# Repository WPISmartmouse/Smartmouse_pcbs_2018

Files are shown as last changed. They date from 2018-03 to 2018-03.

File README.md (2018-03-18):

# BRO Submission README

 - Schematics are included as pdfs
 - BOM is inclded as an excel spreadsheet (some items are approximate)
 - General maze solving methodology is described below

We use a flood-fill algorithm to solve the maze. We explore by taking the optimistic assuming there are no walls other than the ones we have observed up until that point, and replan our next step at each cell. We can return once the center is reached and continue to explore for faster routes as we traverse more of the maze until time runs out or the shortest path is found.

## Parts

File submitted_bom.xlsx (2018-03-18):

Manufctr Part # | Description | Source | Quantity | Cost Per Item | Extended Cost | Purchased | Link for Purchasing | Datasheet | Shipping Included? | Notes
 | 2c Lipo battery | Hobby King | 2 | $7.660 | $15.32 | Y | https://hobbyking.com/en_us/turnigy-nano-tech-1500mah-2s-25-50c-lipo-pack.html |  | No
AS5048A | Magnet Sensor for Encoder | Mouser | 4 | $7.800 | $31.20 |  | https://www.mouser.com/ds/2/588/AS5048_DS000298_3-00-1100510.pdf |  | No | out of stock on Digikey
AS5000-MD6H-2 | Magnet for Encoder | AMS | 4 | $2.900 | $11.60 |  |  | http://ams.com/eng/content/download/14907/272250/12031 | No
 | capacitors | Digikey | 18 | $0.320 | $5.76 |  |  |  | No
 | resistors | Digikey | 22 | $0.050 | $1.10 |  |  |  | No
 | LEDs | Digikey | 16 | $0.400 | $6.40 |  |  |  | No
502443-0270 | CLIK-mate 2mm Pitch 1x2 pcb header | Mouser | 4 | $0.510 | $2.04 |  | https://www.mouser.com/ProductDetail/Molex/502443-0270 | https://www.mouser.com/ds/2/276/5024430270_sd-1074815.pdf | No
502439-0200 | CLIK-mate 2mm Pitch 1x2 crimp housing | Mouser | 4 | $0.150 | $0.60 |  | https://www.mouser.com/ProductDetail/Molex/502439-0200 | https://www.mouser.com/ds/2/276/5024390200_sd-1074810.pdf | No
502438-0100 | CLIK-mate 2mm Pitch terminals | Mouser | 12 | $0.110 | $1.32 |  | https://www.mouser.com/ProductDetail/Molex/502438-0100 | https://www.mouser.com/ds/2/276/5024380100_CRIMP_TERMINALS-179287.pdf | No
502382-0670 | CLIK-mate 1.25mm Pitch 1x6, small conn pcb header | Mouser | 4 | $0.680 | $2.72 |  | https://www.mouser.com/ProductDetail/Molex/502382-0670 | https://www.mouser.com/ds/2/276/5023820670_PCB_RECEPTACLES-179370.pdf | No
502380-0600 | CLIK-mate 1.25mm Pitch 1x6, small conn crimp housing | Mouser | 4 | $0.250 | $1.00 |  | https://www.mouser.com/ProductDetail/Molex/502380-0600?qs=sGAEpiMZZMvyL6eCuHiWiirOw4xo%2ffkY | https://www.mouser.com/ds/2/276/5023800600_CRIMP_HOUSINGS-179295.pdf | No
502382-0370 | CLIK-mate 1.25mm Pitch 1x3 small conn pcb header | Mouser | 14 | $0.540 | $7.56 |  | https://www.mouser.com/ProductDetail/Molex/502382-0370 | https://www.mouser.com/ds/2/276/5023820370_PCB_RECEPTACLES-179354.pdf | No
502380-0300 | CLIK-mate 1.25mm Pitch 1x3 small conn crimp housing | Mouser | 14 | $0.160 | $2.24 |  | https://www.mouser.com/ProductDetail/Molex/502380-0300 | https://www.mouser.com/ds/2/276/5023800300_CRIMP_HOUSINGS-179281.pdf | No
502381-0000 | CLIK-mate 1.25 mm Pitch crimp terminals | Mouser | 66 | $0.044 | $2.90 |  | https://www.mouser.com/ProductDetail/Molex/502381-0000-Loose-Piece | https://www.mouser.com/ds/2/276/5023810000_CRIMP_TERMINALS-179285.pdf | No | bulk discount woot woot
N/A | Teensy 3.6 | Digikey | 1 | $32.500 | $32.50 |  |  |  | No
drv8833 | dual H bridge motor driver | Digikey | 2 | $2.410 | $4.82 |  | https://www.digikey.com/product-detail/en/texas-instruments/DRV8833PWPR/296-29434-1-ND/2743171 | http://www.ti.com/lit/ds/symlink/drv8833.pdf | No
tps82130 | voltage regulator | Digikey | 2 | $5.030 | $10.06 |  | https://www.digikey.com/product-detail/en/texas-instruments/TPS82130SILR/296-47436-1-ND/7708896 | http://www.ti.com/lit/ds/symlink/tps82130.pdf | No
N/A | Mouser shipping | Mouser | 1 | $10.000 | $10.00
N/A | Hobby King shipping | Hobby King | 1 | $8.100 | $8.10
N/A | Digikey shipping | Digikey | 1 | $10.000 | $10.00 |  |  |  | Yes
N/A | Solarbotics RW2i Wheel |  | 2 | $3.950 | $7.90 |  | https://www.pololu.com/product/1127 |  |  | backordered on pololu, alternative is http://www.robotmarketplace.com/products/0-rw2i-3mm.html
VSLY5940 | IR Emitter | Digikey | 14 | $1.500 | $21.00 |  | https://www.digikey.com/products/en?keywords=VSLY5940 | https://www.vishay.com/docs/84240/vsly5940.pdf | No
BPV11F | IR Receiver | Digikey | 14 | $1.080 | $15.12 |  | https://www.digikey.com/products/en?x=0&y=0&lang=en&site=us&KeyWords=BPV11F | https://www.digikey.com/products/en?x=0&y=0&lang=en&site=us&KeyWords=BPV11F | No
 | Custom PCBs |  | 10 | $38.000 | $380.00
3073 | 50:1 Micro Metal Gearmotor HPCB 6V with Extended Motor Shaft | Pololu | 2 | $18.950 | $37.90 |  | https://www.pololu.com/product/3073
 |  |  |  |  | $0.00
 |  |  |  |  | $0.00
 |  |  |  |  | $0.00
 |  |  |  | TOTAL | $613.84

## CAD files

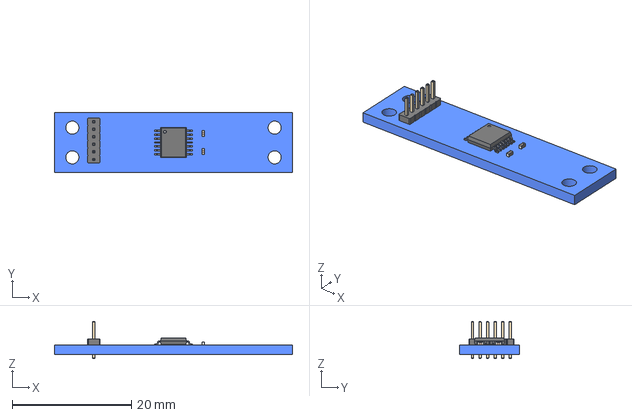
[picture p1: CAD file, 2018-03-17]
encoder_board/encoder_board.step
40.0 x 10.0 x 6.30 mm

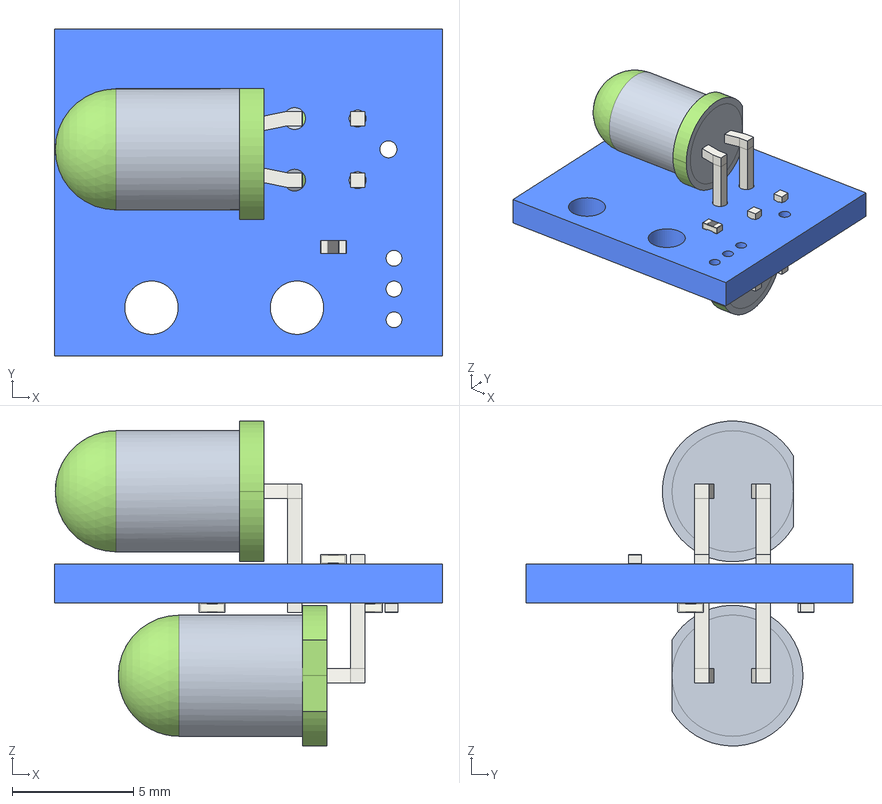
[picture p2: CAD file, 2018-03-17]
sensor_board/sensor_board.step
16.0 x 13.5 x 13.4 mm

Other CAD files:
encoder_board/encoder_board.FCStd
sensor_board/sensor_board.FCStd

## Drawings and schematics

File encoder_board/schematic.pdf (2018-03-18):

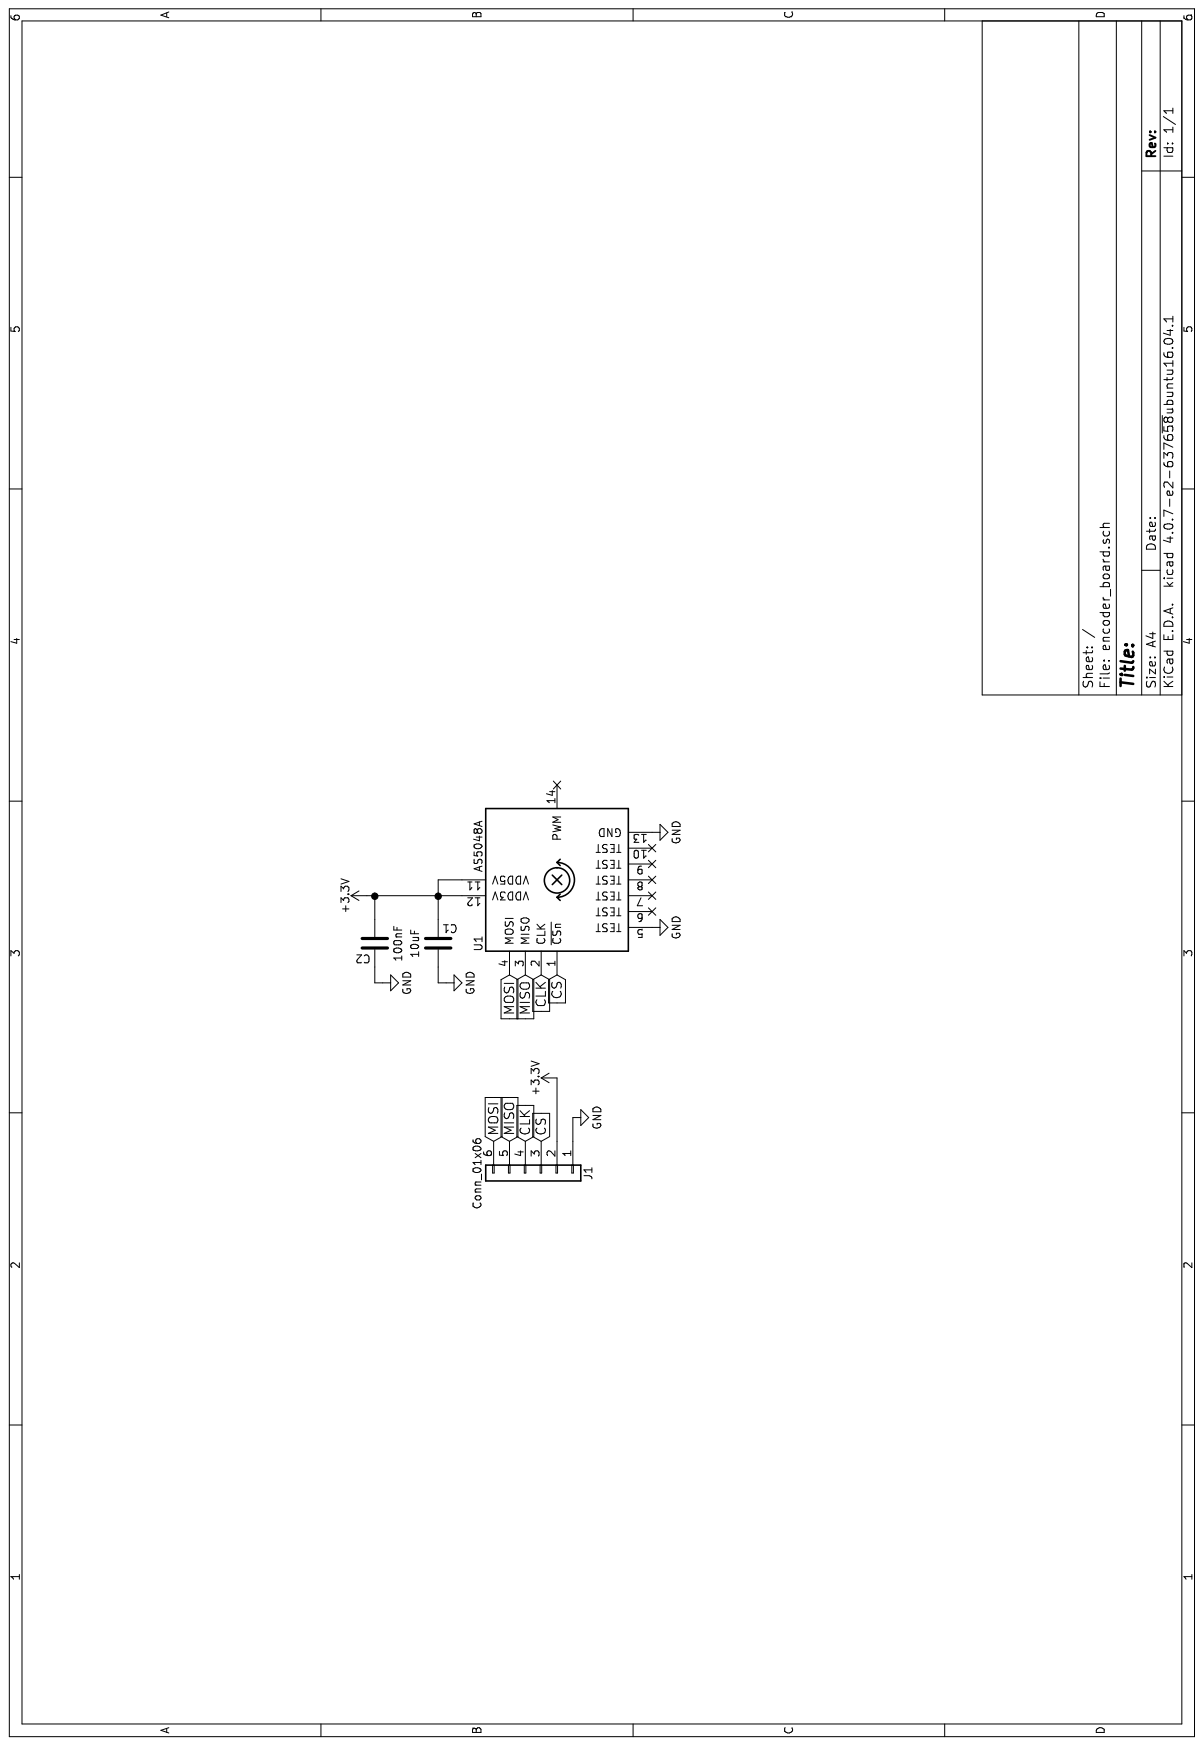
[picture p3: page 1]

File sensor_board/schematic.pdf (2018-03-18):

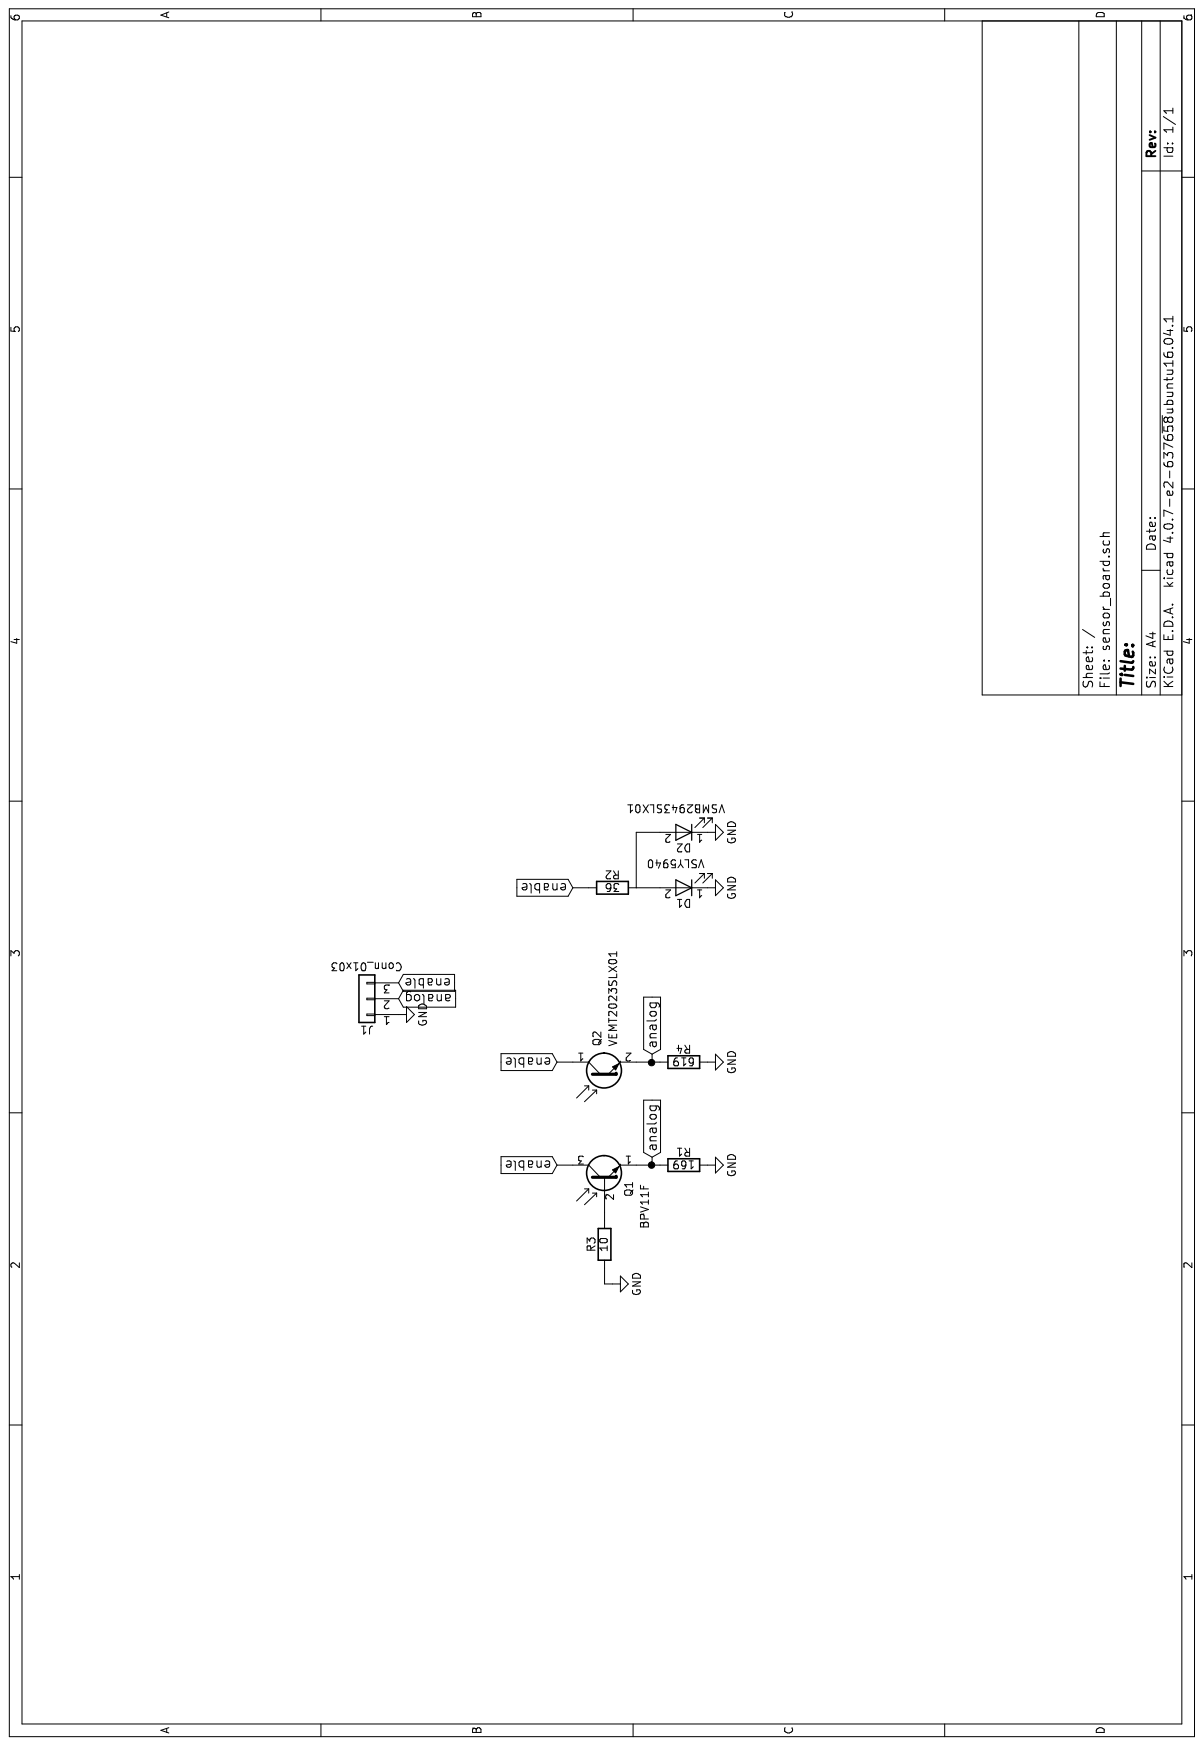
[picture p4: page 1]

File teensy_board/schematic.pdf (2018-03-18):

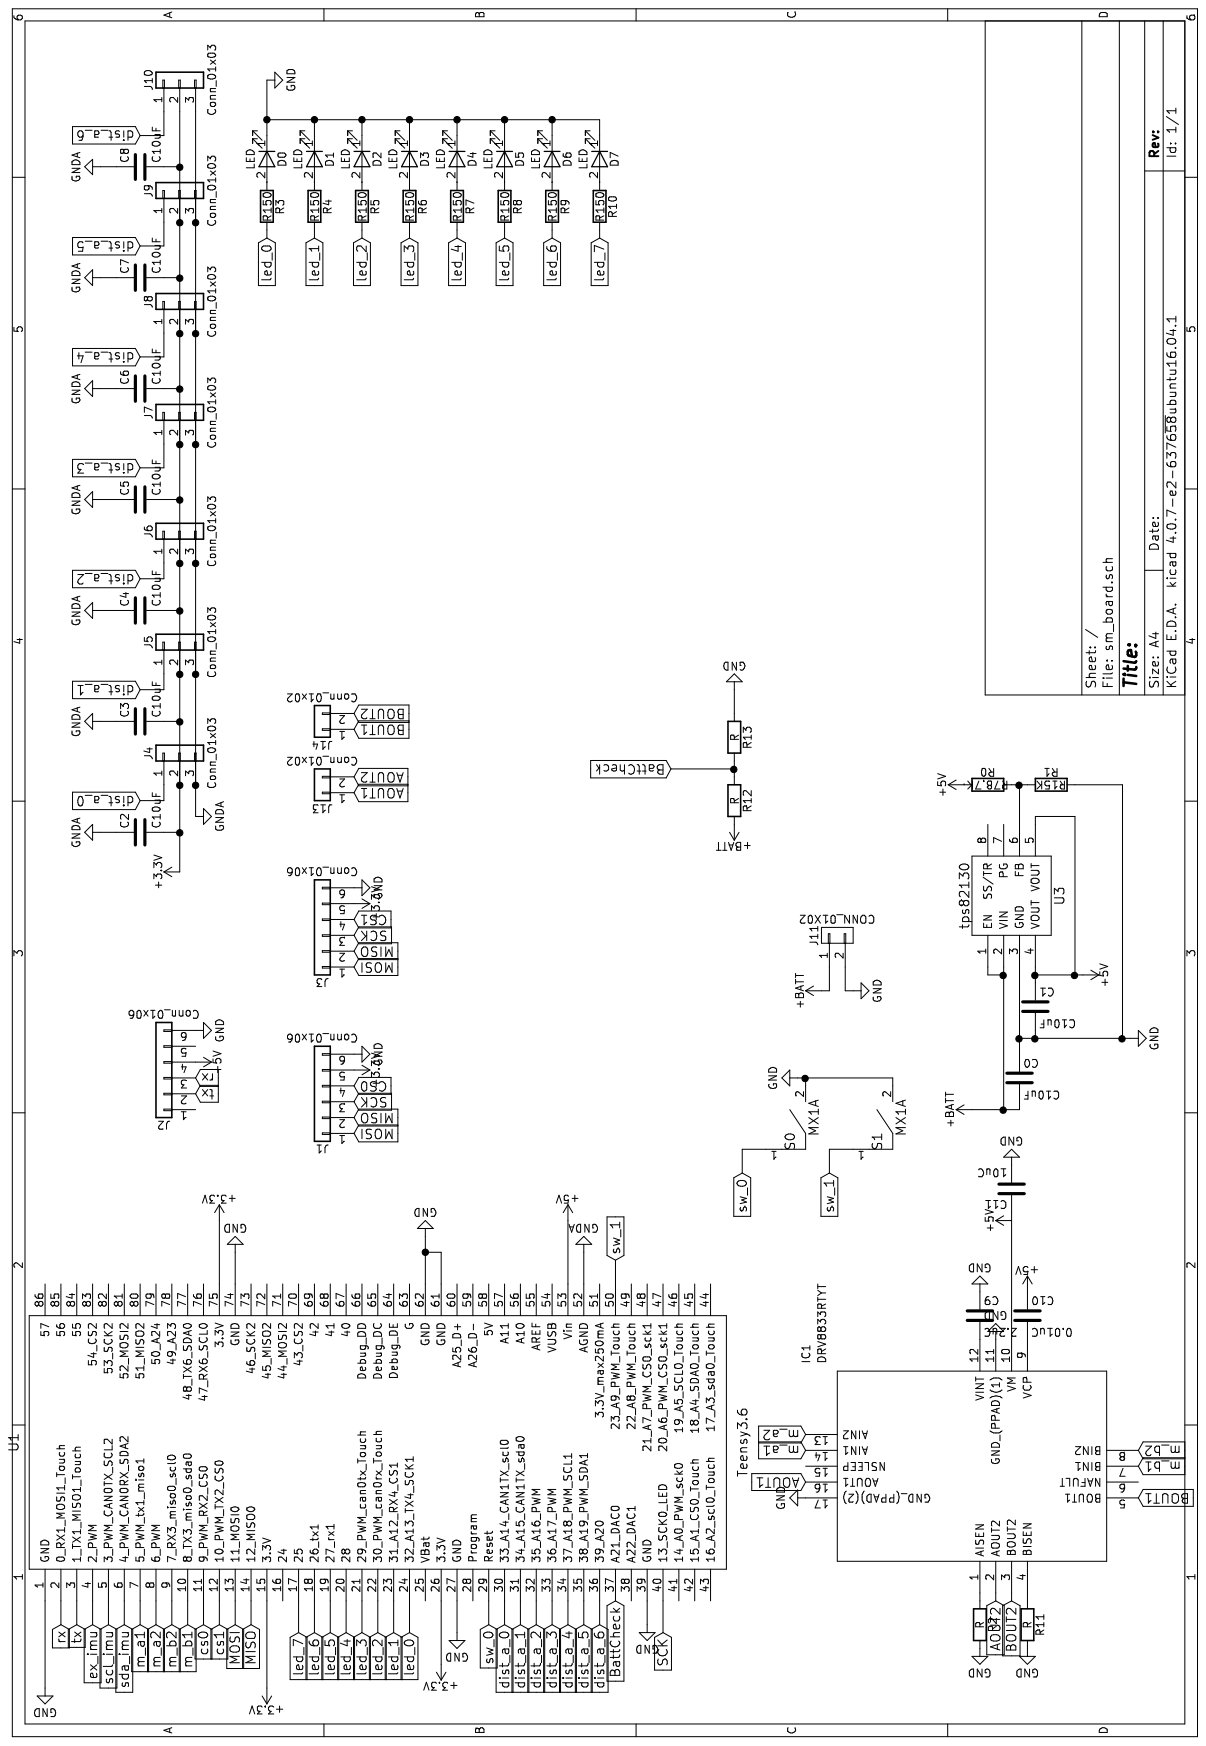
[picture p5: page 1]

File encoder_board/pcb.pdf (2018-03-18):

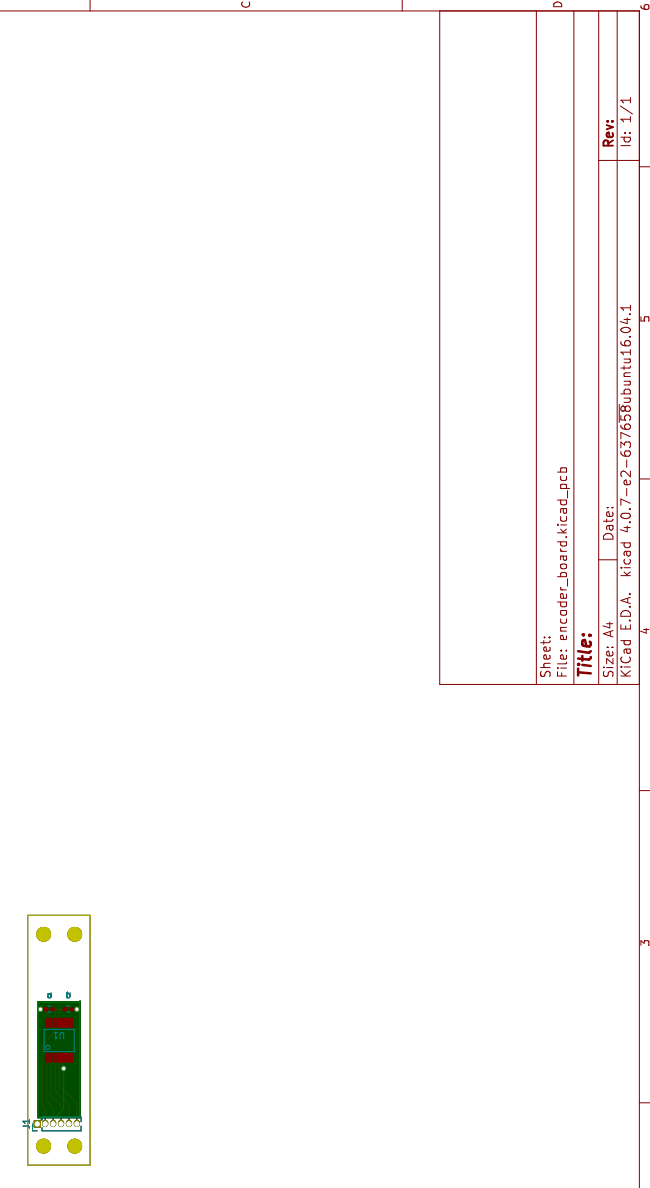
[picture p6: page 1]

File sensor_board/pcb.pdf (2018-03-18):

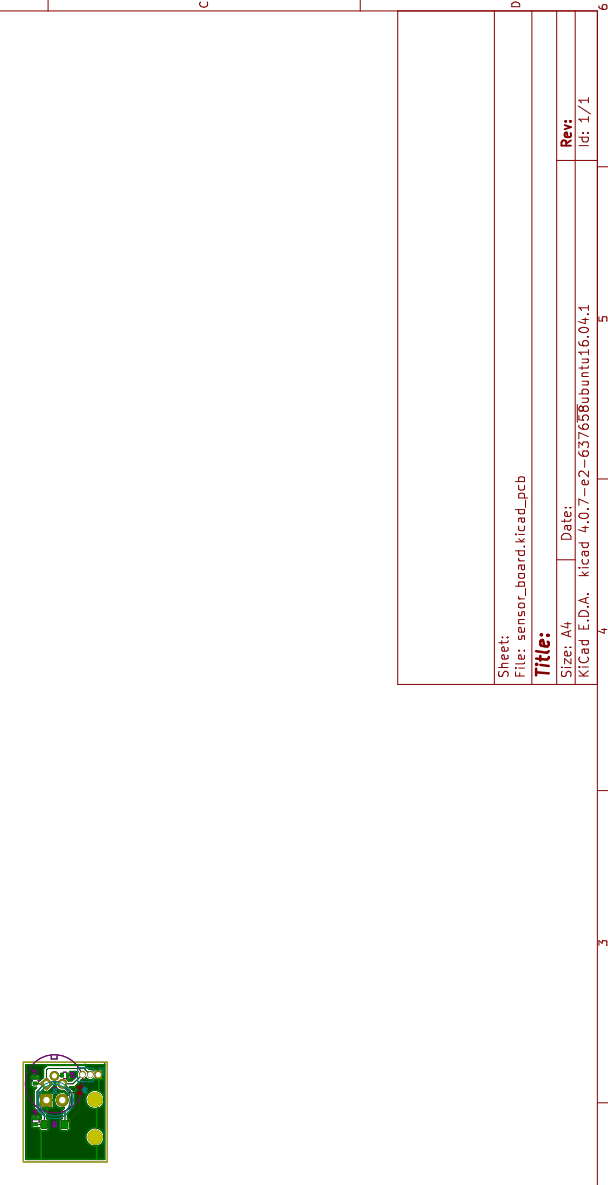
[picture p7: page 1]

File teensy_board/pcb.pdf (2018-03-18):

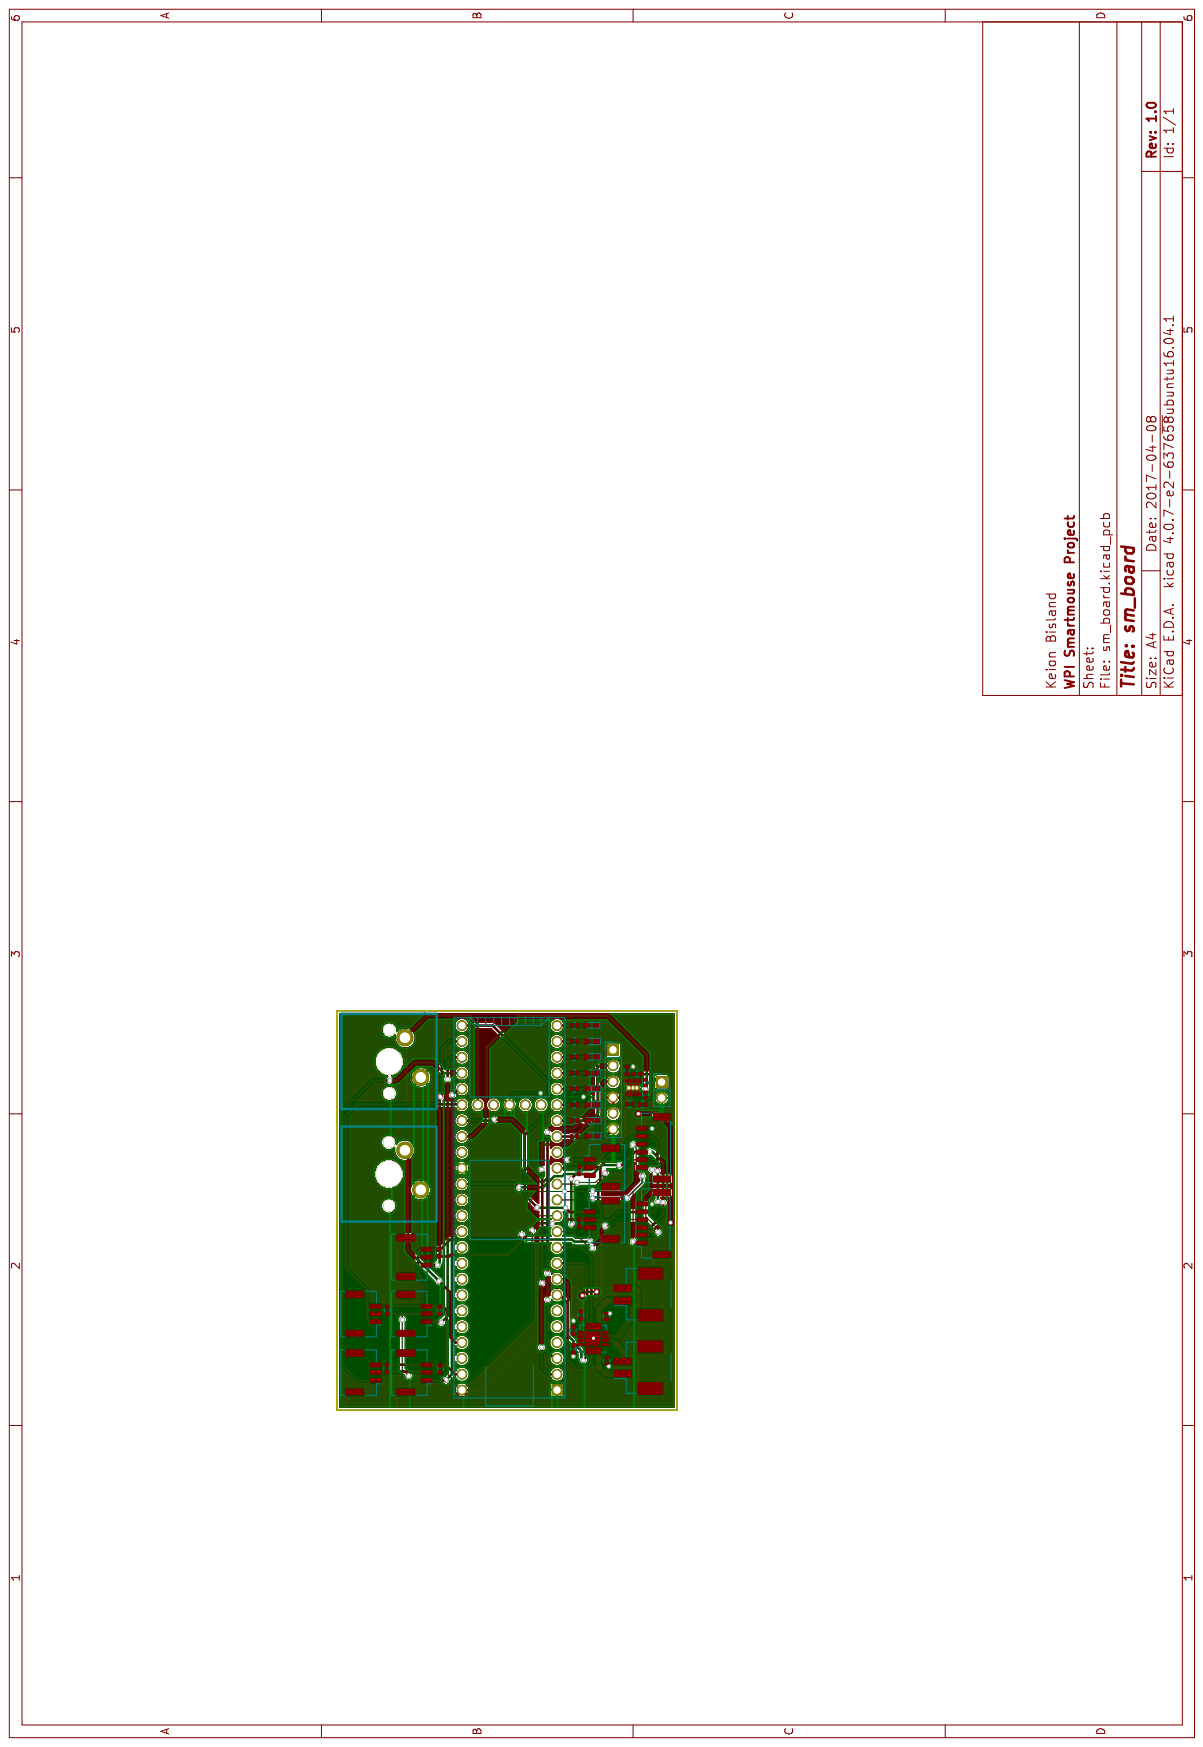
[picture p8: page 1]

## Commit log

2018-03-07 inital commit, 2017 smartmouse board design
    [sm_board.kicad_pcb, sm_board.sch]
2018-03-14 impose new directory structure
    - also commit teensy and mx1a footprint libraries
    [sm_board.kicad_pcb, sm_board.sch]
2018-03-14 basic sensor board
    [sensor_board.kicad_pcb, sensor_board.sch]
2018-03-14 add mounting holes and improve silkscreen
    - board top left is at 100,100
    - overall board size is 7.5mm by 15mm
    [sensor_board.kicad_pcb]
2018-03-14 fix 3d models
    [sensor_board.kicad_pcb]
2018-03-14 Add more board to seperate sensors
    - not sure where mounting holes are?
    - added gerber
    [sensor_board-B.Cu.gbr, sensor_board-B.Mask.gbr, sensor_board-B.SilkS.gbr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]
2018-03-15 change to 1.6mm mounting holes
    - keion said he has them
    - export to STEP for cadding
    [full_sensor_board.step, sensor_board.FCStd, sensor_board.kicad_pcb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]
2018-03-15 add first revision of encoder board
    [encoder_board.kicad_pcb, encoder_board.sch]
2018-03-16 I think im done the schematic for tonight
    [sm_board.kicad_pcb, sm_board.sch]
2018-03-16 pre-meeting board layout
    [_saved_sm_board.sch, sm_board.kicad_pcb]
2018-03-16 add footprint for small ir sensors
    - use 0402 in encoder board
    - still need to switch sensor board
    [encoder_board.kicad_pcb, encoder_board.sch, sensor_board.sch]
2018-03-16 change 3d models to use /usr/share/kicad when possible
    [sensor_board.kicad_pcb]
2018-03-16 fix grid origin and tweaked placement
    - added nice dimension indicators
    [encoder_board.kicad_pcb]
2018-03-17 redo sensor board
    - supports any combo of the two types of sensors
    [sensor_board.kicad_pcb, sensor_board.sch]
2018-03-17 make board symetrical and longer
    [encoder_board.kicad_pcb]
2018-03-17 use named nets
    [encoder_board.kicad_pcb, encoder_board.sch]
2018-03-17 redo pcb shape to match CAD changes
    [encoder_board.kicad_pcb]
2018-03-17 generate step for encoder board
    [encoder_board.FCStd, encoder_board.kicad_pcb, encoder_board.step]
2018-03-17 move ground plane to back
    - rexport encoder step
    [encoder_board.FCStd, encoder_board.kicad_pcb, encoder_board.step]
2018-03-17 apply cosine's suggestions about gnd plane
    [encoder_board.kicad_pcb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]
2018-03-17 rexport sensor board
    - use LED shape for both for better cadding
    [full_sensor_board.step, sensor_board.FCStd, sensor_board.kicad_pcb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]
2018-03-17 I think this is done
    [_saved_sm_board.sch, sm_board.kicad_pcb, sm_board.sch]
2018-03-17 removed random hole
    [sm_board.kicad_pcb]
2018-03-17 reviewer final encoder board.
    [encoder_board.kicad_pcb, encoder_board.sch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]
2018-03-17 added gerber files
    [sm_board.kicad_pcb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]
2018-03-17 final review of sensor board
    [sensor_board-B.Cu.gbr, sensor_board-B.Mask.gbr, sensor_board-B.SilkS.gbr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]
2018-03-17 Moved files into gerber folder
    [sm_board-B.Cu.gbr, sm_board-B.SilkS.gbr, sm_board-Edge.Cuts.gbr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]
2018-03-17 After review meeting
    [sm_board.kicad_pcb, sm_board.sch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]
2018-03-17 regenerate gerber
    [encoder_board-B.Cu.gbr, encoder_board-B.SilkS.gbr, encoder_board-F.Cu.gbr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]
2018-03-17 regenerated with edge cuts and f/b mask
    [encoder_board.kicad_pcb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]
2018-03-17 Boards that got ordered
    [sm_board.kicad_pcb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]
2018-03-18 finish submission materials
    [submitted_bom.xlsx]
